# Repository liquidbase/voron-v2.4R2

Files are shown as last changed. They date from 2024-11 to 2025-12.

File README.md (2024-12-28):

# voron v2.4 R2 Pro
Buildlog of voron v2.4 R2 from start to finish with all modifications and finally the toolchanger.

Where possible, corresponding build videos are also included in the readme. When what was done and which files were used will be noted in any case.

# Videolog

# Buildlog
26.11.2024
- Initial Structure for GitHub

15.12. - 23.12.2024
- Printerbuild
- Squaring Gantry

24.12.2024
- Configuration of Klipper
- Squaring Gantry

25.12.2024
- Fixed Motorposition and Stepper
- Squaring Gantry

27.12.2024
- Squaring Gantry

# Configlog
23.12.2024
- Initial config

24.12.2024
- Added UUIDs for documentation
- Heater & fan check with configuration
- Fixed motor pins for Z
- Set homing speed
- Separate macros to own file

25.12.2024
- Splitted Files
- Input Shaper
- Added KAMP
- Thermistor for Chamber
- Fan Control
- Fixed motor settings

27.12.2024
- Update config with new run_current & microsteps
- Update print_start macro

26.12.2024
- Fixed Extrudersettings
- Raised Retries for QDL

27.12.2024
- Added nozzlewiper (by MarcFair)
- Fixed Z-Offset

# Filelog
26.11.2024
- Added formbot specific docs

27.11.2024
- Added PiCam-Mount
- Added Panellatch

01.12.2024
- Added voron assembly manual
- Added CAD file
- Added sample configs for M8P
- Added printfiles for Z-Drives. Z-Idlers & Z-Endstop
- Added 3MF file for Z-Drives
- Added list for parts to print

09.12.2024
- Added printfiles for front idlers
- Added 3MF for front idlers

10.12.2024
- Added printfiles for XY Joints
- Added 3MF for XY Joints

11.12.2024
- Added printfiles for Gantry
- Added 3MF for Gantry

12.12.2024
- Added printfiles for Z-Joints
- Added 3MF for Z-Joints
- Added printfiles for tools
- Added 3MF for tools

22.12.2024
- Added print files for alle parts

23.12.2024
- Added printer.cfg
- Added nevermore print files

24.12.2024
- Added ebb36.cfg

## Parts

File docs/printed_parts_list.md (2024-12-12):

### Voron 2.4 Printed Parts List

List of parts to print for [Voron 2.4](https://github.com/VoronDesign/Voron-2) organized by the [Assembly Manuals](https://github.com/VoronDesign/Voron-2/blob/Voron2.4/Docs/2.4_Assembly_Manual.pdf) order of assembly, allowing for just-in-time printing of parts while building the printer.  Configuration is standard Voron 2.4 (Afterburner Direct Feed, DIN rail mounts) with choices for E3D, Dragon or Mosquito hot ends on a 250mm, 300mm or 350mm frame.  No parts for the drag chain are included, as often these are purchased parts rather than printed.

Names of the sections (such as `Gantry/X_Axis/XY Joints`) match the name of the [STL directory](https://github.com/VoronDesign/Voron-2/tree/Voron2.4/STLs/VORON2.4) that contains the prints.  Note that Voron Design uses filenames starting with `[a]_` at the start of a filename to indicate parts that can be printed in an accent color.

_Credit to [krobertson](https://gist.github.com/krobertson/adfd96689e8b66e7e122705c9ac6bb21) for making a Gist of all parts. This Gist is a modified version of that list, organized by order of assembly, removed parts that don't need printing, identified parts that are optional or specific to a build, and fixed a few incorrect part listings._

--------------------------------------------------------------------------------

### Frame (page 10)

#### [Tools](https://github.com/VoronDesign/Voron-2/tree/Voron2.4/STLs/VORON2.4/Tools)

```
[ x ]  [ x ]   rail_installation_guide_center_x2.stl
```

--------------------------------------------------------------------------------

### Z Drive Assembly (page 18)

#### [Z_Drive](https://github.com/VoronDesign/Voron-2/tree/Voron2.4/STLs/VORON2.4/Z_Drive)

```
[ x ]  [ x ]   [a]_belt_tensioner_a_x2.stl
[ x ]  [ x ]   [a]_belt_tensioner_b_x2.stl
[ x ]  [ x ]   [a]_z_drive_baseplate_a_x2.stl
[ x ]  [ x ]   [a]_z_drive_baseplate_b_x2.stl
[ x ]  [ x ]   z_drive_main_a_x2.stl
[ x ]  [ x ]   z_drive_main_b_x2.stl
[ x ]  [ x ]   z_drive_retainer_a_x2.stl
[ x ]  [ x ]   z_drive_retainer_b_x2.stl
[ x ]  [ x ]   z_motor_mount_a_x2.stl
[ x ]  [ x ]   z_motor_mount_b_x2.stl
```

#### [Z_Idlers](https://github.com/VoronDesign/Voron-2/tree/Voron2.4/STLs/VORON2.4/Z_Idlers)

_There are two different GT20 20T pully files; only one set of them should be printed_

```
[ x ]  [ x ]  [ x ]  [ x ]   [a]_z_tensioner_x4_9mm.stl
[ x ]  [ x ]               z_tensioner_bracket_a_x2.stl
[ x ]  [ x ]               z_tensioner_bracket_b_x2.stl
```

#### [Z_Endstop](https://github.com/VoronDesign/Voron-2/tree/Voron2.4/STLs/VORON2.4/Z_Endstop)

```
[ x ]   nozzle_probe.stl
```

--------------------------------------------------------------------------------

### AB Drive Modules (page 38)

#### [Gantry/Front_Idlers](https://github.com/VoronDesign/Voron-2/tree/Voron2.4/STLs/VORON2.4/Gantry/Front_Idlers)

```
[ X ]   [a]_tensioner_left.stl
[ X ]   [a]_tensioner_right.stl
[ x ]   front_idler_left_lower.stl
[ x ]   front_idler_left_upper.stl
[ x ]   front_idler_right_lower.stl
[ x ]   front_idler_right_upper.stl
```

#### [Gantry/AB_Drive_Units](https://github.com/VoronDesign/Voron-2/tree/Voron2.4/STLs/VORON2.4/Gantry/AB_Drive_Units)

```
[ x ]         [a]_cable_cover.stl
[ x ]  [ x ]   [a]_z_chain_retainer_bracket_x2.stl
[ x ]         a_drive_frame_lower.stl
[ x ]         a_drive_frame_upper.stl
[ x ]         b_drive_frame_lower.stl
[ x ]         b_drive_frame_upper.stl
```

--------------------------------------------------------------------------------

### Gantry (page 46)

#### [Gantry/X_Axis/XY Joints](https://github.com/VoronDesign/Voron-2/tree/Voron2.4/STLs/VORON2.4/Gantry/X_Axis/XY_Joints)

_Select one endstop_pod_* , and one xy_joint_cable_bridge_* depending on your hardware kit_

```
[ x ]   [a]_endstop_pod_microswitch.stl <- select one ^^^ (microswitch XY endstops)
[ x ]   [a]_xy_joint_cable_bridge_generic.stl <= select one vvv (generic drag chain)
[ x ]   xy_joint_left_lower.stl
[ x ]   xy_joint_left_upper.stl
[ x ]   xy_joint_right_lower.stl
[ x ]   xy_joint_right_upper.stl
```

#### [Gantry](https://github.com/VoronDesign/Voron-2/tree/Voron2.4/STLs/VORON2.4/Gantry)

```
[ x ]  [ x ]  [ x ]  [ x ]   [a]_z_belt_clip_lower_x4.stl
[ x ]  [ x ]  [ x ]  [ x ]   [a]_z_belt_clip_upper_x4.stl
[ x ]                     z_chain_bottom_anchor.stl
[ x ]                     z_chain_guide.stl              <-- Not in CAD or documentation
```

--------------------------------------------------------------------------------

### Afterburner (page 58)

#### [Gantry/X_Axis/X Carriage](https://github.com/VoronDesign/Voron-2/tree/Voron2.4/STLs/VORON2.4/Gantry/X_Axis/X_Carriage)

```
[  ]  [  ]   [a]_belt_clamp_x2.stl
[  ]         [a]_blower_housing_front.stl
[  ]         blower_housing_rear.stl
[  ]         hotend_fan_mount.stl
[  ]         probe_retainer_bracket.stl
[  ]         x_carriage_frame_left.stl
[  ]         x_carriage_frame_right.stl
[  ]         x_carriage_pivot_block.stl
```

#### [Gantry/X_Axis/X Carriage/Printheads/E3D V6](https://github.com/VoronDesign/Voron-2/tree/Voron2.4/STLs/VORON2.4/Gantry/X_Axis/X_Carriage/Printheads/E3D_V6)

_Select only one printhead; this is for E3D_

```
[  ]   printhead_front_e3dv6.stl
[  ]   printhead_rear_e3dv6.stl
```

#### [Gantry/X_Axis/X Carriage/Printheads/Slice Mosquito](https://github.com/VoronDesign/Voron-2/tree/Voron2.4/STLs/VORON2.4/Gantry/X_Axis/X_Carriage/Printheads/Slice_Mosquito)

_Select only one printhead; this is for Slice Mosquito_

```
[  ]   printhead_front_mosquito.stl
[  ]   printhead_rear_mosquito.stl
```

#### [Gantry/X_Axis/X Carriage/Printheads/TriangleLab Dragon](https://github.com/VoronDesign/Voron-2/tree/Voron2.4/STLs/VORON2.4/Gantry/X_Axis/X_Carriage/Printheads/TriangleLab_Dragon)

_Select only one printhead; this is for Phaetus Dragon_

```
[  ]   printhead_front_dragon.stl
[  ]   printhead_rear_dragon.stl
```

#### [Gantry/X_Axis/X Carriage/Direct Feed](https://github.com/VoronDesign/Voron-2/tree/Voron2.4/STLs/VORON2.4/Gantry/X_Axis/X_Carriage/Direct_Feed)

_Select the chain anchor (generic or igus) that matches your drag chain choice_ 

```
[  ]   [a]_connector_cover.stl
[  ]   [a]_guidler.stl
[  ]   [a]_latch.stl
[  ]   chain_anchor_generic.stl <-- select one vvv (generic drag chain)
[  ]   chain_anchor_igus.stl    <-- select one ^^^ (igus drag chain)
[  ]   extruder_body.stl
[  ]   extruder_motor_plate.stl
[  ]   latch_shuttle.stl
```

--------------------------------------------------------------------------------

### Belting Z Drive (page 78)

#### [Gantry/Z_Joints](https://github.com/VoronDesign/Voron-2/tree/Voron2.4/STLs/VORON2.4/Gantry/Z_Joints)

```
[ x ]  [ x ]  [ x ]  [ x ]   z_joint_lower_x4.stl
[ X ]                     z_joint_upper_hall_effect.stl <-- if using hall effect XY
[ x ]  [ x ]  [ x ]  [ x ]   z_joint_upper_x4.stl <-- use x3 if using hall effect XY
```

--------------------------------------------------------------------------------

###  LCD Module (page 82)

#### [Electronics_Compartment/LCD_Module](https://github.com/VoronDesign/Voron-2/tree/Voron2.4/STLs/VORON2.4/Electronics_Compartment/LCD_Module)

```
[  ]   [a]_mini12864_case_hinge.stl
[  ]   mini12864_case_front.stl
[  ]   mini12864_case_rear.stl
[  ]   mini12864_spacer.stl
```

--------------------------------------------------------------------------------

### Skirts (page 86)

#### [Electronics_Compartment/Plug_Panel](https://github.com/VoronDesign/Voron-2/tree/Voron2.4/STLs/VORON2.4/Electronics_Compartment/Plug_Panel)

```
[  ]   plug_panel_filtered_mains.stl
```

#### [Skirts](https://github.com/VoronDesign/Voron-2/tree/Voron2.4/STLs/VORON2.4/Skirts)

```
[  ]  [  ]   [a]_60mm_fan_blank_insert_x2.stl
[  ]  [  ]   [a]_belt_guard_a_x2.stl
[  ]  [  ]   [a]_belt_guard_b_x2.stl
[  ]  [  ]   side_fan_support_x2.stl
```

#### [350](https://github.com/VoronDesign/Voron-2/tree/Voron2.4/STLs/VORON2.4/Skirts/350)

_Use these skirts when printing a 350mm frame_

```
[  ]  [  ]   front_rear_skirt_a_350_x2.stl
[  ]  [  ]   front_rear_skirt_b_350_x2.stl
[  ]  [  ]   side_skirt_a_350_x2.stl
[  ]  [  ]   side_skirt_b_350_x2.stl
```

--------------------------------------------------------------------------------

### Panels (page 94)

#### [Panel_Mounting/Front_Doors](https://github.com/VoronDesign/Voron-2/tree/Voron2.4/STLs/VORON2.4/Panel_Mounting/Front_Doors)

```
[  ]  [  ]  [  ]  [  ]   door_hinge_x4.stl
[  ]  [  ]               handle_a_x2.stl
[  ]  [  ]               handle_b_x2.stl
[  ]  [  ]               latch_x2.stl
```

#### [Panel_Mounting](https://github.com/VoronDesign/Voron-2/tree/Voron2.4/STLs/VORON2.4/Panel_Mounting)

```
[  ]  [  ]  [  ]  [  ]                                                   bottom_panel_clip_x4.stl
[  ]  [  ]                                                               bottom_panel_hinge_x2.stl
[  ]  [  ]  [  ]  [  ]  [  ]  [  ]  [  ]  [  ]  [  ]  [  ]  [  ]  [  ]   corner_panel_clip_3mm_x12.stl  <-- 3mm no foam, 6mm w/foam
[  ]  [  ]  [  ]  [  ]                                                   corner_panel_clip_6mm_x4.stl   <-- print either the 3mm or
[  ]  [  ]  [  ]  [  ]  [  ]  [  ]  [  ]  [  ]  [  ]  [  ]  [  ]  [  ]   midspan_panel_clip_3mm_x12.stl <-- the 6mm set 
[  ]  [  ]  [  ]                                                         midspan_panel_clip_6mm_x3.stl  <--  
[  ]  [  ]                                                               z_belt_cover_a_x2.stl
[  ]  [  ]                                                               z_belt_cover_b_x2.stl
```

--------------------------------------------------------------------------------

### Spool Holder (page 102)

#### [Spool_Management](https://github.com/VoronDesign/Voron-2/tree/Voron2.4/STLs/VORON2.4/Spool_Management)

```
[  ]   bowen_retainer.stl
[  ]   spool_holder.stl
```

--------------------------------------------------------------------------------

### Exhaust Filter (page 106)

#### [Exhaust_Filter](https://github.com/VoronDesign/Voron-2/tree/Voron2.4/STLs/VORON2.4/Exhaust_Filter)

```
[  ]         [a]_filter_access_cover.stl
[  ]  [  ]   [a]_exhaust_filter_mount_x2.stl
[  ]         exhaust_filter_grill.stl
[  ]         exhaust_filter_housing.stl
```

--------------------------------------------------------------------------------

### Electronics Mounting (page 112)

#### [Electronics_Compartment/DIN_Brackets](https://github.com/VoronDesign/Voron-2/tree/Voron2.4/STLs/VORON2.4/Electronics_Compartment/DIN_Brackets)

_There are a number of different brackets here depending on your electronics selection._

```
[  ]  [  ]         duet_duex_bracket_x2.stl
[  ]               lrs_psu_bracket_clip.stl
[  ]  [  ]  [  ]   pcb_din_clip_x3.stl
[  ]  [  ]         ramps_bracket_x2.stl
[  ]               raspberrypi_bracket.stl
[  ]               rs25_psu_bracket_clip.stl
[  ]  [  ]         skr_1.3_bracket_x2.stl
[  ]  [  ]         skr_mini_e2_bracket_x2.stl
[  ]  [  ]         skr_mini_e3_bracket_x2.stl
```

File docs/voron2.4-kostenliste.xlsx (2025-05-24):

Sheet: Gesamt
Gesamtkosten
voron 2.4 | 1580.08
Toolchanger | 2022.31
Gesamt: | 3602.39

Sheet: voron 2.4
 |  |  | 1580.08 €
Part | Preis | Bemerkung
Kit | 800.43 € | Startkit
EBB36 | 14.87 € | Dragonburner
Filament | 151.77 € | Verkleidung
Magnetfolie | 51.96 €
Filament | 50.60 € | Verkleidung
Satin Printplate 255x255 | 54.00 € | Druckplatte für X1C zum drucken von PC/PBT
Sherpa Mini Metall Kit | 92.97 € | Extruder
Motor Assembly | 43.13 € | Ersatz
Linear Rail 50mm Tap | 15.00 € | Ersatz
Lüfter | 27.98 € | Ersatz
Kabel | 37.78 € | 220V
Kabel | 49.89 € | Motor
Kabel | 39.97 € | Motor
Bearings | 27.97 € | Gantry-Mod
Phaetus Rapido Plus Hotend 2 HF | 98.99 € | Hotend-Ersatz
Hardend Nozzle 0.4 | 1.99 €
OptoTap | 20.78 € | Ersatz

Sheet: Toolchanger
 |  |  |  |  | 2022.31 €
Part | Menge | Einzelpreis | Preis | Bemerkung
Phaetus Rapido Plus Hotend 2 HF (https://www.3djake.de/phaetus/rapido-plus-hotend-2-hf?sai=15275) | 5 | 98.99 € | 494.95 €
Bondtech OEM Set für Sherpa Mini RIDGA V2 (https://www.3djake.de/bondtech/oem-set-fuer-sherpa-mini-ridga-v2?sai=17363) | 5 | 41.99 € | 209.95 €
Moons Nema 14 Schrittmotor 17mm Dicke 10 Zahn (https://meltbro.de/moon-nema-14-schrittmotor-17mm-dicke-fuer-voron-2-4-sherpa-orbiter-galileo-extruder.html) | 3 | 29.99 € | 89.97 €
MOAR_CAN (https://alchemy3d.de/products/moar_can-8-9-port-can-hub-by-isik-s-tech?_pos=1&_sid=7aa387c65&_ss=r) | 1 | 32.50 € | 32.50 €
BIGTREETECH EBB 36 (https://biqu.equipment/products/bigtreetech-ebb-36-42-can-bus-for-connecting-klipper-expansion-device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) | 4 | 15.75 € | 63.00 €
Filament Runout Sensor | 5 | 9.99 € | 49.95 €
Alu-Extrusions | 1 | 89.29 € | 89.29 € | Top Hat
Igus CANBus Chainflex CF9.02.06 | 1 | 28.79 € | 28.79 €
Kleinteile | 1 | 43.91 € | 43.91 € | Tap Changer
Filament PC/PBT | 4 | 50.99 € | 203.96 €
Filament ASA | 1 | 25.98 € | 25.98 €
Werkzeug | 1 | 49.00 € | 49.00 €
Kleinteile | 1 | 37.63 € | 37.63 € | Stealth Changer
Kleinteile | 1 | 22.04 € | 22.04 € | Silikon, Stahldraht, Federn
Lüfter | 1 | 53.73 € | 53.73 €
Optotap | 5 | 11.79 € | 58.95 €
Alu-Extrusions | 1 | 9.93 € | 9.93 €
Kleinteile | 10 | 0.90 € | 9.00 € | Federstahldraht
Acrylplatten | 1 | 23.79 € | 23.79 € | Top Hat
USB-Hub | 1 | 17.99 € | 17.99 €
TungstenCarbid Nozzle | 5 | 55.00 € | 275.00 €
Flexplate Satin | 1 | 70.00 € | 70.00 €
Flexplate Structured PEI | 1 | 63.00 € | 63.00 €

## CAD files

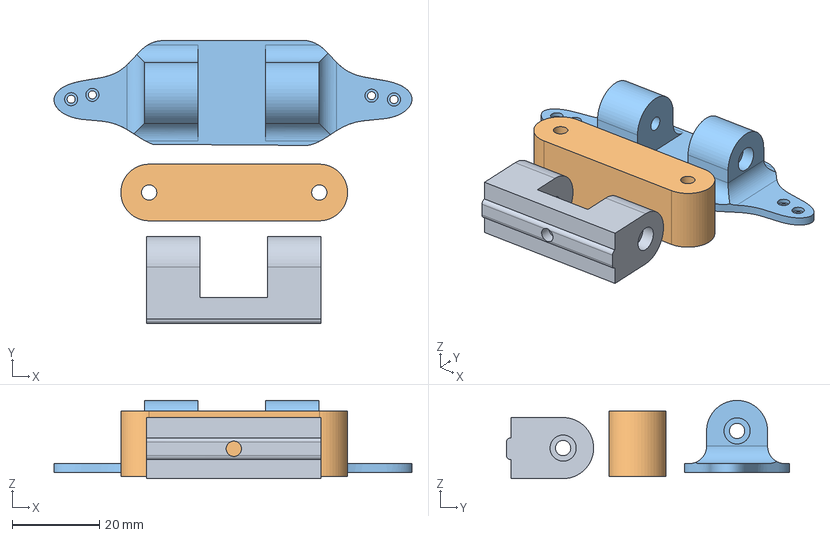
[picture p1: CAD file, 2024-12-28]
printfiles/misc/C92X_PsycHoShafts_Mount by PsychoShaft/CAD/Voron_C92X_Camera_Complete.step
82.1 x 64.9 x 17.9 mm

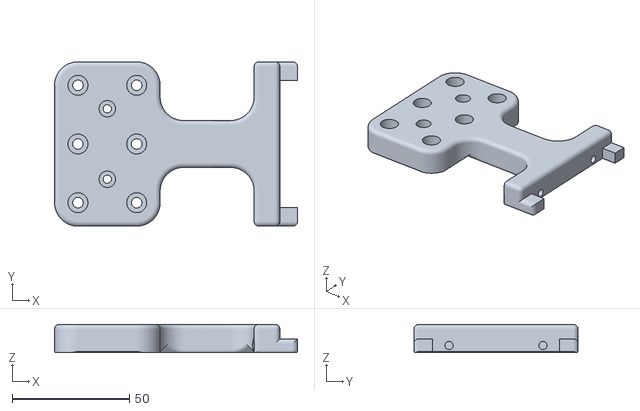
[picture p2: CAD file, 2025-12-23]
printfiles/Toolchanger/DraftShiftCableManagement/UserMods/FlisherOfatale/PTFE_Breakout_Block/Flisher-PTFE_Breakout_Block_Main-v3.1.stl
103.5 x 70.0 x 12.0

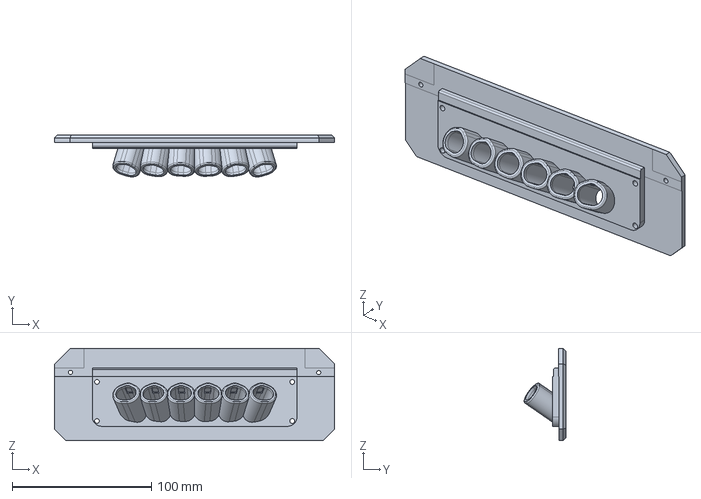
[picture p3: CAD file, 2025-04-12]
printfiles/Toolchanger/DraftShiftCableManagement/UserMods/seenit783/SV08 Umbilical Back Plate/Main Body SV08 Umbilical.step
200.8 x 30.0 x 66.0 mm

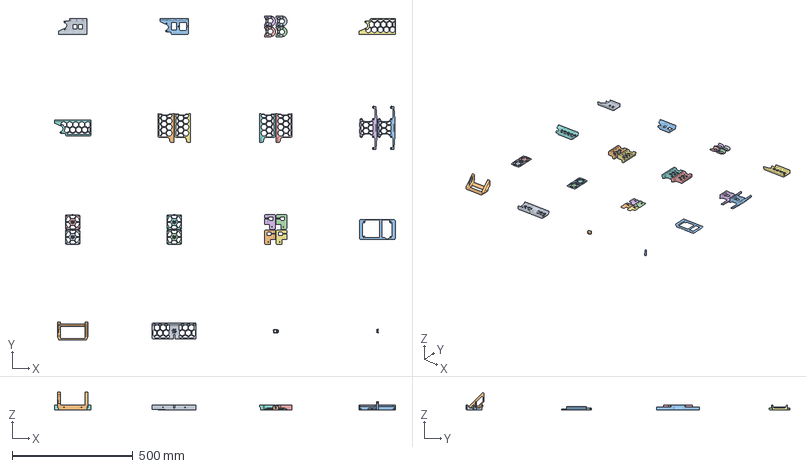
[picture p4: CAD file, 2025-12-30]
printfiles/xx_skirt_assembly.3mf
1410.5 x 1339.9 x 72.4 mm
keystone_panel.stl
BTT HDMI5 V1_2 mount bracket_Regular.stl
btt-hdmi5-v1_2-mount-frame_voron-logo.stl
z_belt_cover_b_x2.stl x 2
[a]_fan_grill_b_x2.stl x 2
z_belt_cover_a_x2.stl x 2
[a]_fan_grill_a_x2.stl x 2
side_fan_support_x2.STL x 2
side_skirt_b_350_x2.stl x 2
side_skirt_a_350_x2.stl x 2
[a]_belt_guard_b_x2.stl x 2
power_inlet_filtered.stl
[a]_belt_guard_a_x2.stl x 2
front_skirt_a_350.stl
front_skirt_b_350.stl
V2 Rear skirt 350 with cable cutout.stl
keystone_wlan.stl
Thermistor_Mount_2020_5mm.stl

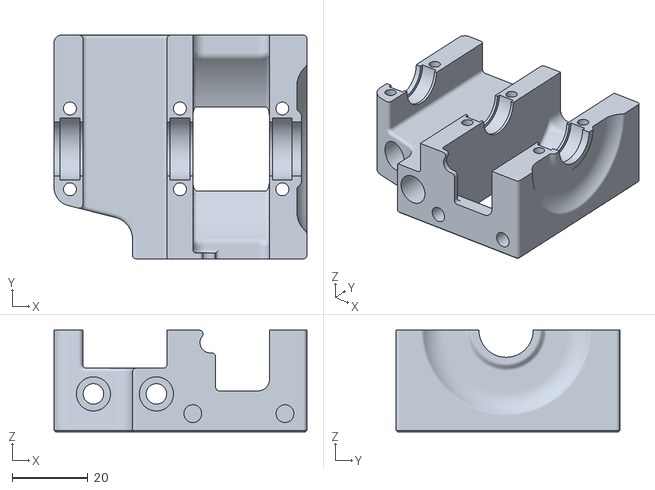
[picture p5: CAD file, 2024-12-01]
printfiles/Z_Drive/z_drive_main_b_x2.stl
66.7 x 59.0 x 26.8

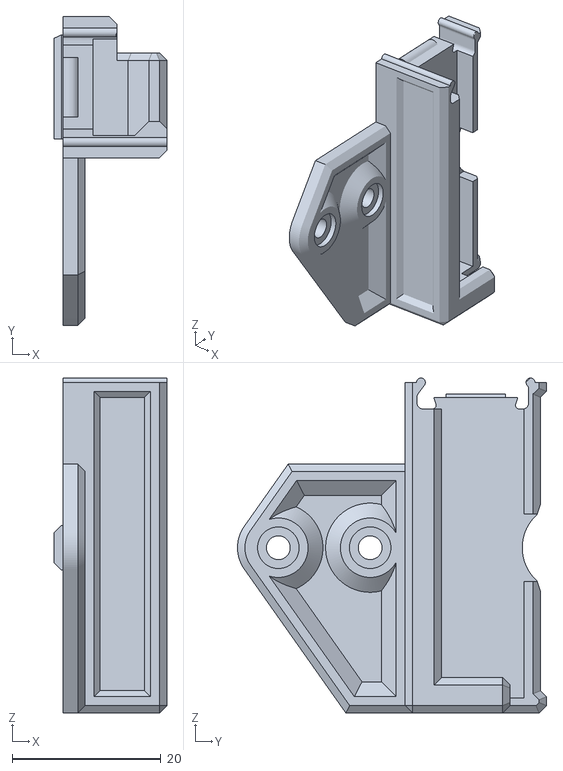
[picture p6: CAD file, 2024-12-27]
printfiles/misc/voron-24-nozzle-cleaning-brush-model_files/nozzle-cleaning-brush-main-body.stl
15.2 x 41.6 x 45.1

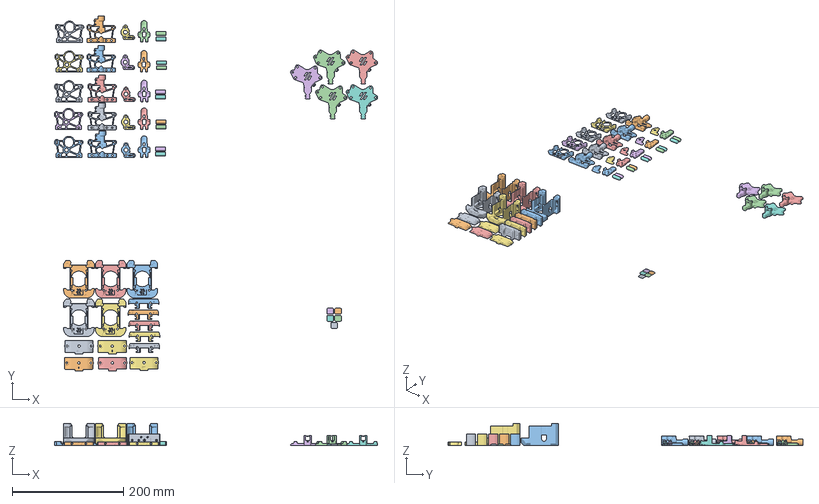
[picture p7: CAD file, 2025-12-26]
printfiles/xx_Toolhead_assembly.3mf
580.7 x 637.5 x 40.0 mm
housing_rear_x1_rev17.STL x 5
[c]_Voron_Diffuser.stl x 5
dragon_cowl_6_magnets_v6.step x 5
EBB_G2SA.step x 5
Sherpa_Mini_Mount.stl x 5
housing_core_std^housing_sherpa_mini_a3_r16(FDM)(FilamentSensor)(ECAS04) x 5
RapidoHF_Mount.stl x 5
18.0mm_oct_universal_spacer.stl x 10
[a]_idler_arm_long_x1_rev16a.STL x 5
[a]_housing_front_x1_rev15.STL x 5

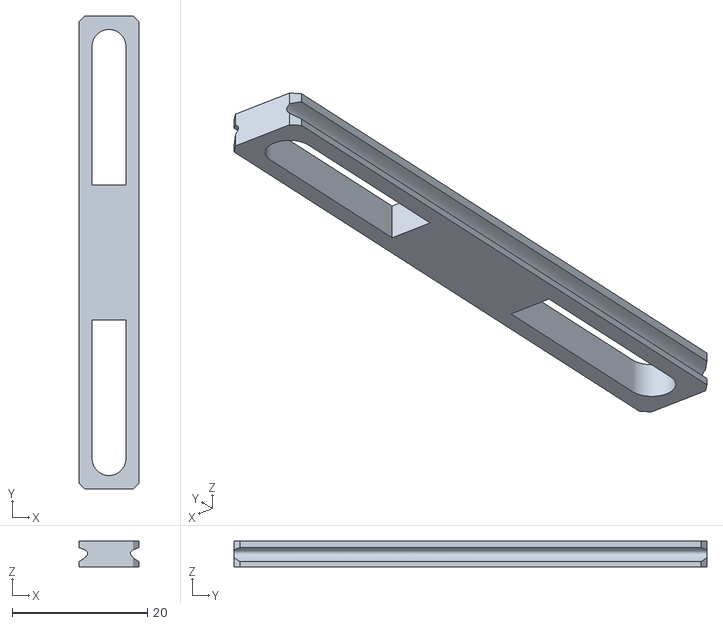
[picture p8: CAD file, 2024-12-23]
printfiles/tap/MGN9_Assembly_Tool.stl
8.90 x 70.0 x 3.80

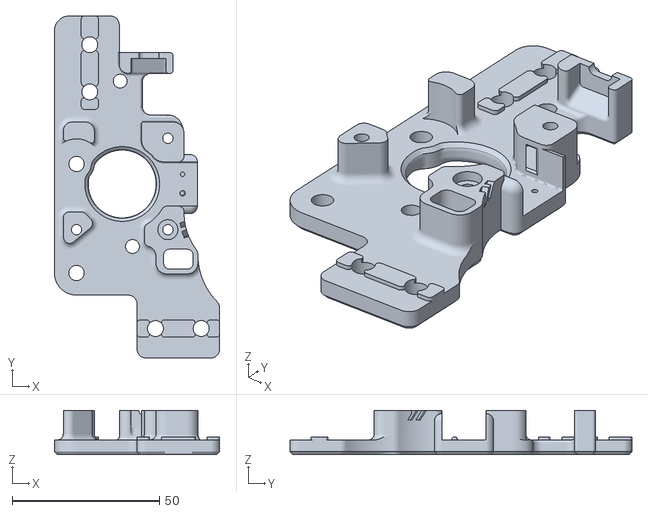
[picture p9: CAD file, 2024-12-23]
printfiles/AB_Drive_Units/a_drive_frame_upper_with_jst_y_endstop.stl
56.0 x 116.0 x 15.0

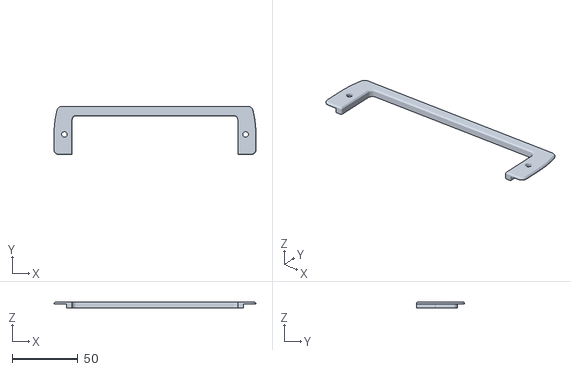
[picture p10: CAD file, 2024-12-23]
printfiles/backplate/Front_Plate.stl
154.0 x 36.8 x 4.60

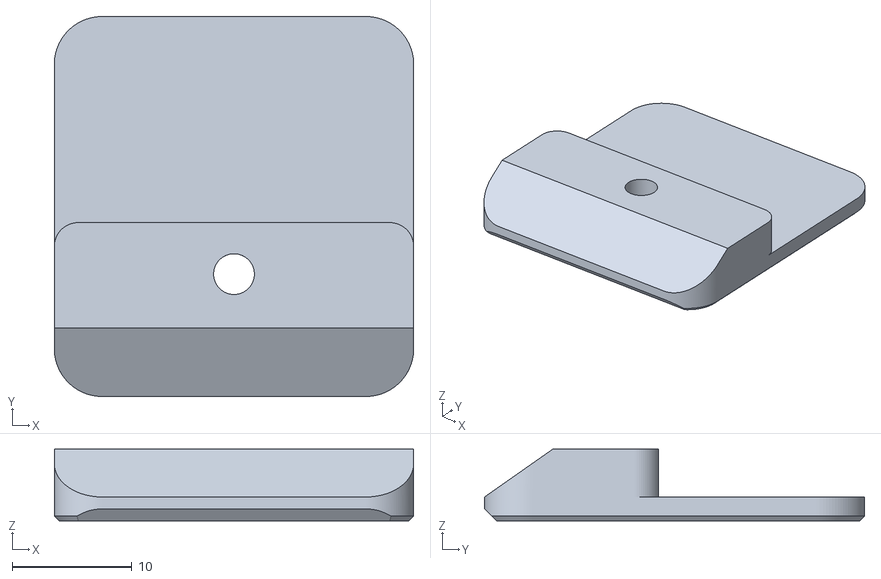
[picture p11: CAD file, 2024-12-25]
printfiles/bottom_panel/bottom_panel_clip_x4.stl
30.0 x 31.7 x 6.00

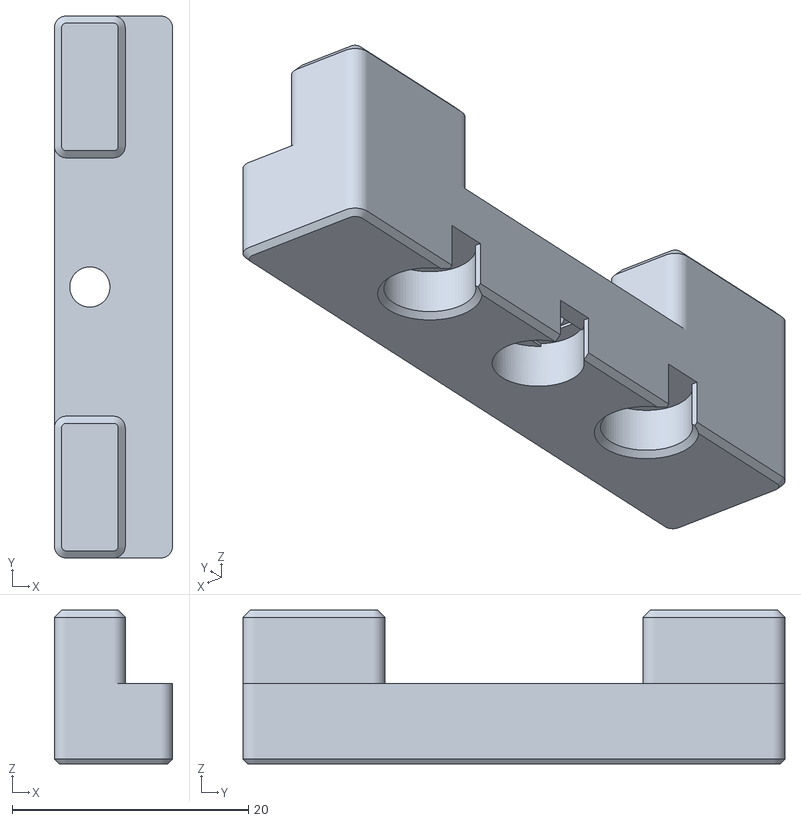
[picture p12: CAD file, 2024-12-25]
printfiles/Doors/latch_x2.stl
10.0 x 45.9 x 13.0

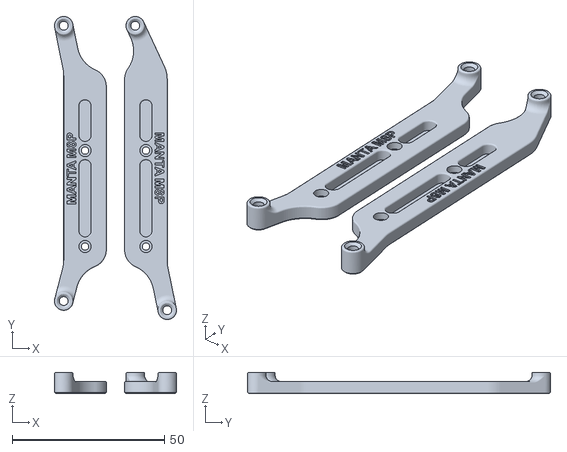
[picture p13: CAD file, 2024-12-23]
printfiles/EBay/Manta_M8P_2pc.stl
40.1 x 99.5 x 7.00

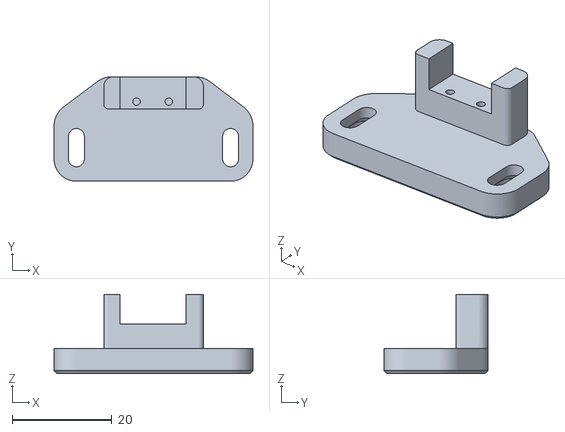
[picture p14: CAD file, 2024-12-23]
printfiles/Endstops/y_endstop.stl
40.0 x 21.0 x 15.9

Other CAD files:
printfiles/Z_Drive/z_drive_main_a_x2.stl
printfiles/Front Idlers/front_idler_right_lower.stl
printfiles/Gantry/[a]_z_belt_clip_upper_x4.stl
printfiles/misc/C92X_PsycHoShafts_Mount by PsychoShaft/STL/C92X_Extrusion_Bracket_No_Support_Required.stl
printfiles/AB_Drive_Units/[a]_cable_cover.stl
printfiles/AB_Drive_Units/[a]_z_chain_retainer_bracket_x2.stl
printfiles/AB_Drive_Units/a_drive_frame_lower.stl
printfiles/AB_Drive_Units/a_drive_frame_upper.stl
printfiles/AB_Drive_Units/b_drive_frame_lower.stl
printfiles/AB_Drive_Units/b_drive_frame_upper.stl
printfiles/Doorbuffer.3mf
printfiles/Doors/Door_Handle_x1.STL
printfiles/Doors/door_hinge_x6.stl
printfiles/Doors/handle_a_x2.stl
printfiles/Doors/handle_b_x2.stl
printfiles/EBay/PSU_stabilizer_50mm.stl
printfiles/EBay/Printed_Part_for_CAN_Cable_V1.2.stl
printfiles/EBay/lrs_200_psu_bracket_x2.stl
printfiles/EBay/pcb_din_clip_x3.stl
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

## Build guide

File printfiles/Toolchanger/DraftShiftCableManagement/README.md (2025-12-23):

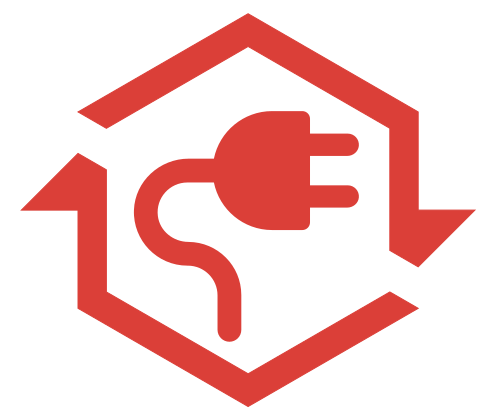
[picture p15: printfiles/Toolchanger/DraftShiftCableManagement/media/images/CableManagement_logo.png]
#  CableManagement


&nbsp;&nbsp;&nbsp;&nbsp;&nbsp;&nbsp;


Backpacks, Umbilicals, and general cable management projects
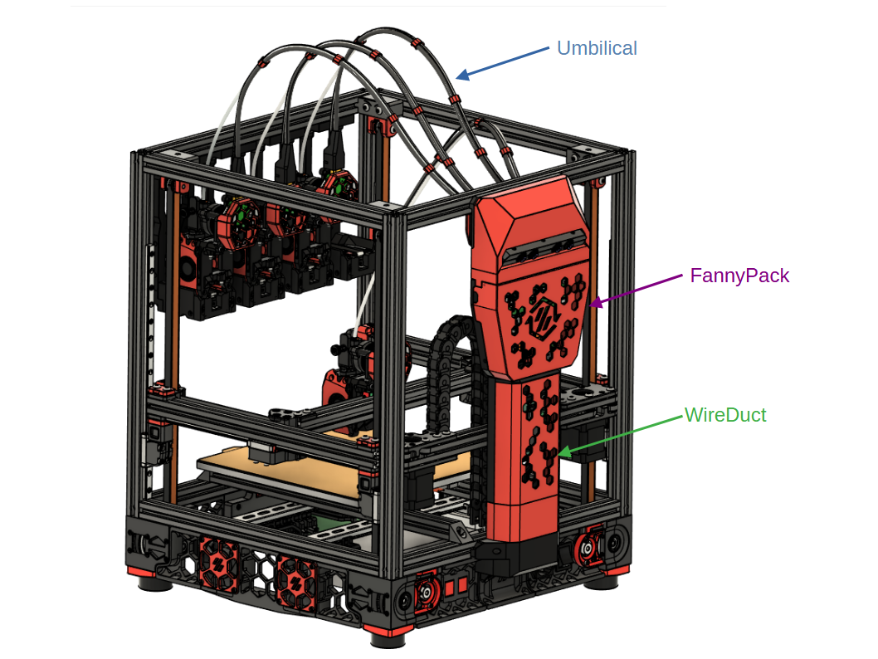
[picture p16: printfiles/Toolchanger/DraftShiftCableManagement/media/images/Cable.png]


This repo will be a collection of different options.  Feel free to use the one that you prefer.

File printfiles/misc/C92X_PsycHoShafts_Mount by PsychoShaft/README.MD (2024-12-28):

# Important Notes

Hello everyone,

Here is my C920 camera mod, please follow the disasembly guide below to remove the current mount off the camera. Please keep the 4 bottom screws from the mount as you will need them for my mod.

# Instructions For Disassembly

[Found Here!](https://www.ifixit.com/Guide/Logitech+C920+Webcam+Disassembly/115077)
#

This mod allows you to set 2 point postion for your camera, 

## BOM

Qty | Item
:-- | :--
2 | M3x40mm
1 | M3x10mm
2 | Nuts
1 | M3 Hammerhead nut



# Photos of finished build below

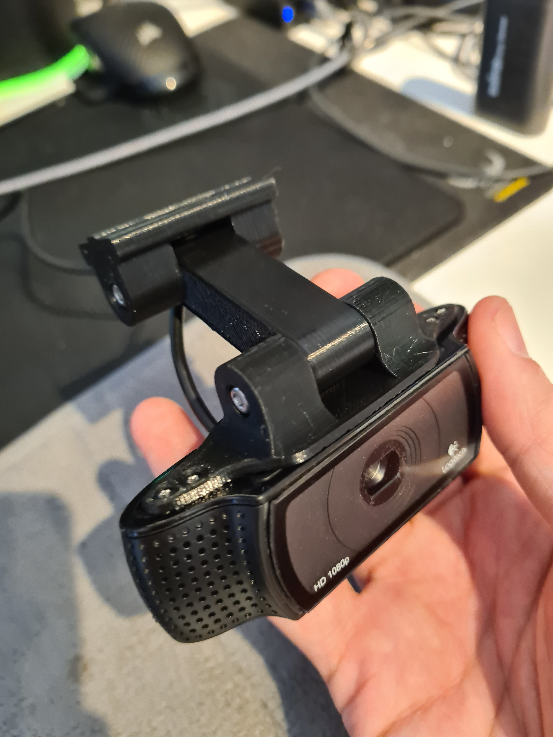
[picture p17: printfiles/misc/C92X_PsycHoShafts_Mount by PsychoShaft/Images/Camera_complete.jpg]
 
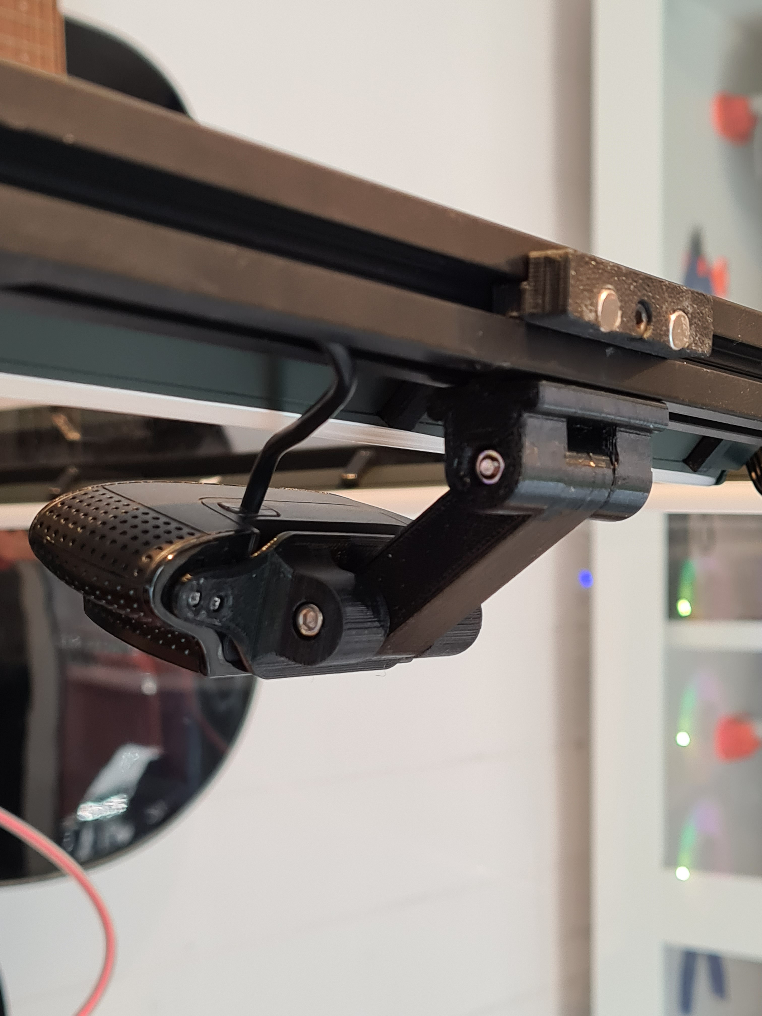
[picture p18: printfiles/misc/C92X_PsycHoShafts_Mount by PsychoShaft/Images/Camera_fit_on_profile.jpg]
 
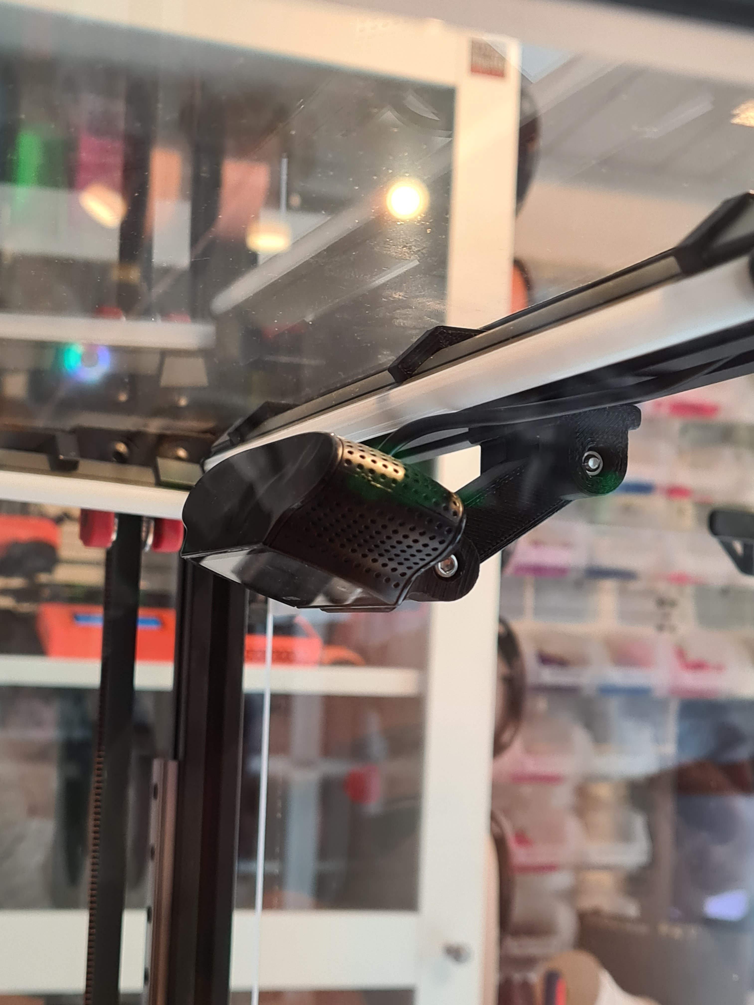
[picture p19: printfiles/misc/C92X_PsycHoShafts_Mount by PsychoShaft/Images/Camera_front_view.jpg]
 
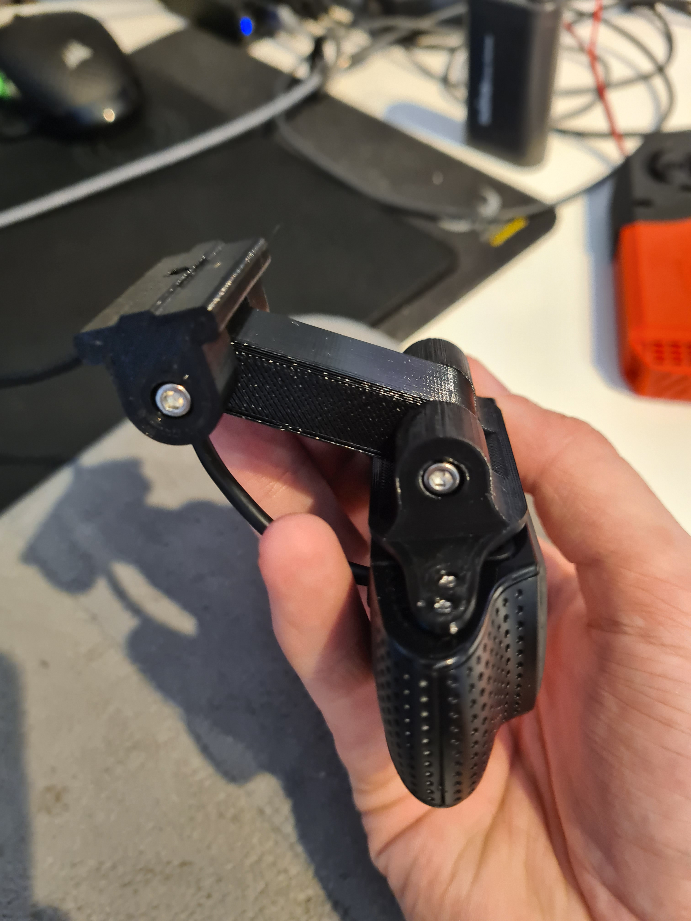
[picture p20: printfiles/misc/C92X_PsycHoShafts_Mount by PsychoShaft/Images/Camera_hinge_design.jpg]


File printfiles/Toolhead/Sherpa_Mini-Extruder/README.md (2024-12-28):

## Sherpa Mini - Release 2:

This release adds support for Bondtech's RIDGA v2 in addition to numerous tweaks and updates to make the extruder easier to work on and more reliable than ever. 

## Changelog

+ Bondtech RIDGA v2 compatibility (R2 RC1 and newer)
+ Bondtech insert support
+ Stronger and stiffer idler arm
+ Increased clearance between idler arm and core
+ Minor fixes and adjustments in preparation for upcoming upgrades

+ Core housing and rear housing need to be reprinted if upgrading from Release 1
+ Updated idler arms are backwards compatible with Release 1 and Release 2 RC1

## FAQ
For Material Requirements, Print Settings and How to Interpret the file naming structure, please see: "Print_Settings_and_File_Key.txt"

The BOM and Sourcing Guide for this product can be found here: https://docs.google.com/spreadsheets/d/1O3eyVuQ6M4F03MJSDs4Z71_XyNjXL5HFTZr1jsaAtRc/edit?usp=sharing

## Product Info
This is the Sherpa Mini Extruder, a ground up design developed by Anlin and the team at Annex Engineering. It's a dual geared hobbed filament extruder designed for use with any printer. It features a gear driven design to provide torque while being able to be near silent. You must perform your own tuning to get the best results.

A Pinion Equipped Pancake Stepper is required for this Release.

Our discord server can be found here: 

Join me on Discord (https://discord.gg/MzTR3zE)

Please only use GitHub Issues for repo and file related problems. For general design related questions and technical support please visit our Discord server.

Image of Sherpa Extruder

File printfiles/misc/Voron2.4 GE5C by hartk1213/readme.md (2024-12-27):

# Voron 2.4 GE5C Z joint  

##

### BOM
Screws			
|Size|Qty|
|---|---|
|M3x12 |4|
|M3x16 or M3x20 SHCS|16|	
|M5x20 |4|	
|Ge5C Bearing|4|
|M5x1mm spacer|4|
|If using Halleffect 6x3 magnet | 1 |

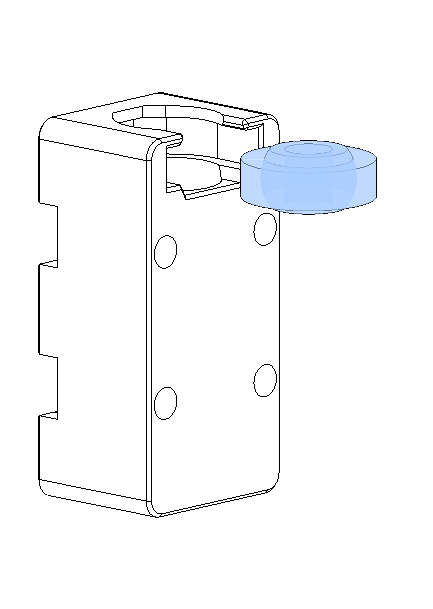
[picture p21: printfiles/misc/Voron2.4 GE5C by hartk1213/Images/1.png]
 

First just insert GE5C bearing , it should just pop in

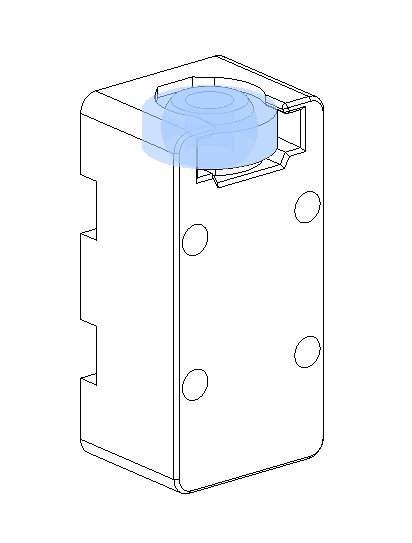
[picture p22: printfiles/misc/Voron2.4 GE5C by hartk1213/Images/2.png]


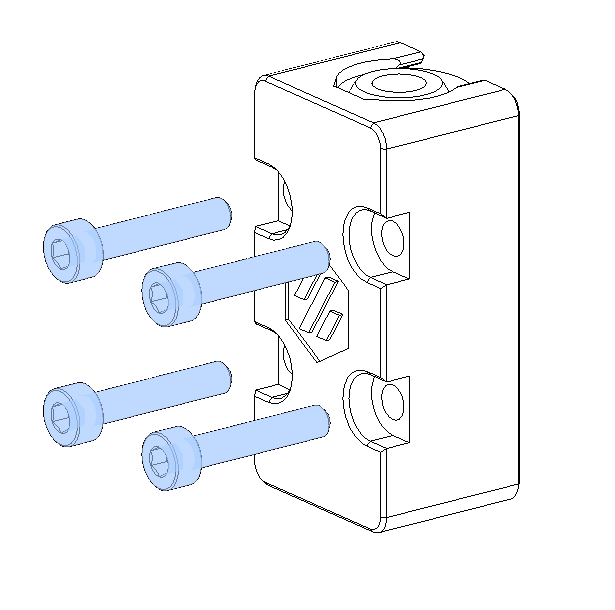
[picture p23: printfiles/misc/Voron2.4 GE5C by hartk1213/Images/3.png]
 

Now if you are using the "slim" version you need 4 m3x16 screws per z joint, if you are using the standard or hall effect version then you need 4 m3x20 per z joint.

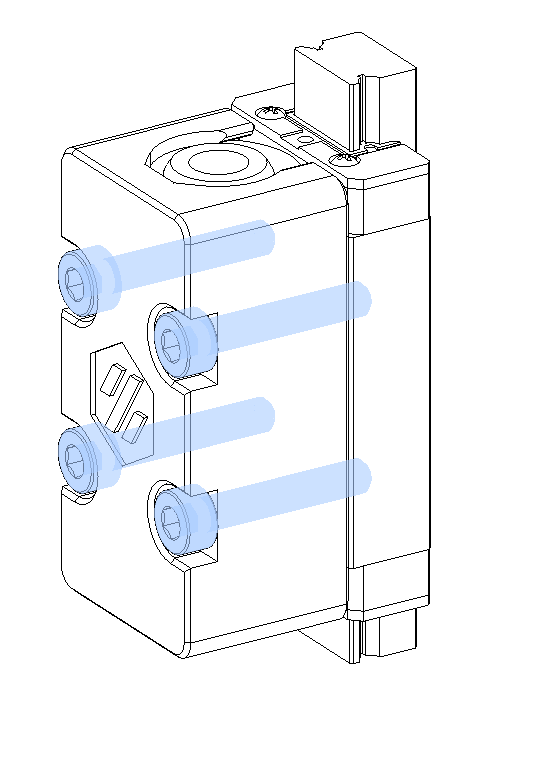
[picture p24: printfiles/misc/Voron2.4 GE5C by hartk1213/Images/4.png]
 

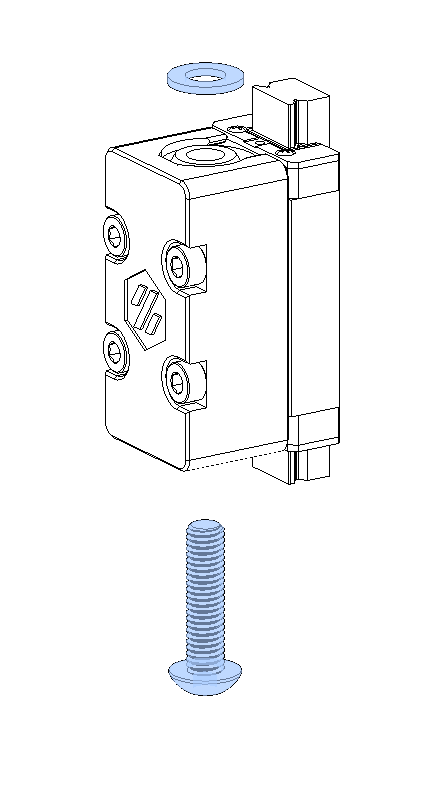
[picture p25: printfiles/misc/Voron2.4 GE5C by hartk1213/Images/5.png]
 

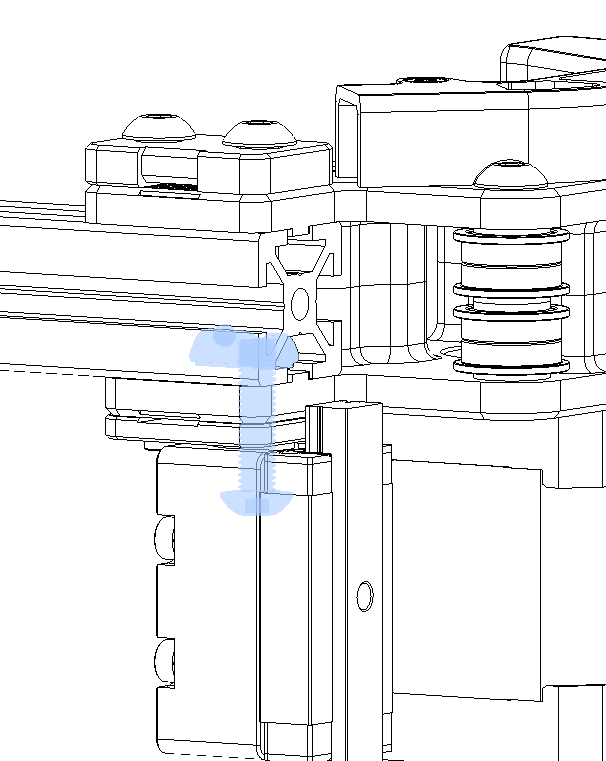
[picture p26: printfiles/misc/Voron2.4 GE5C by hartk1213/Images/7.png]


Use an M5x20 BHCS and 1 m5x1mm washer and screw it into the gantry using a roll in tnut

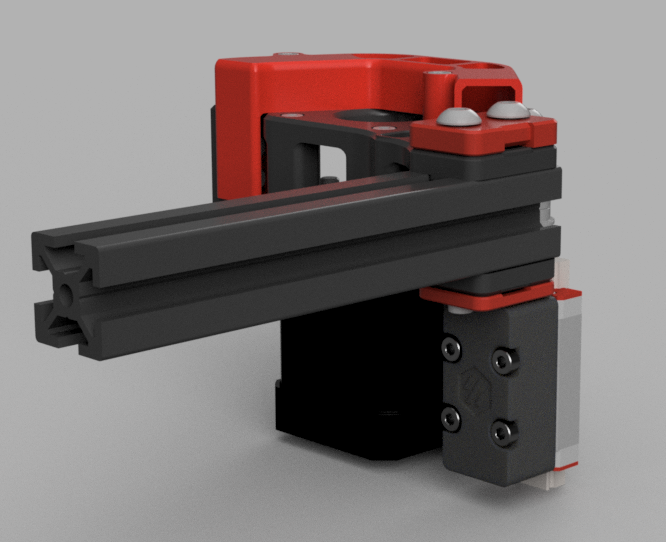
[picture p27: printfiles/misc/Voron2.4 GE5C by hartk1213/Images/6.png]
 

This is how it should be assembled when all done

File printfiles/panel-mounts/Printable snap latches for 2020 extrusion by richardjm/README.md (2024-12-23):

# Printable quick release latch for panels on 2020 extrusion

*I wouldn't say no to a like and a make on printables if you're that way inclined -
https://www.printables.com/model/172368-voron-24-filament-latch-or-any-2020-extrusion*

## Intro

This is originally inspired by a youtube video - [https://www.youtube.com/watch?v=6p7M18oPn3k](https://www.youtube.com/watch?v=6p7M18oPn3k)

Another user is creating cad and variants - [https://github.com/v6cl/My-Voron2.4-Customs/tree/main/Panel_Locker](https://github.com/v6cl/My-Voron2.4-Customs/tree/main/Panel_Locker)

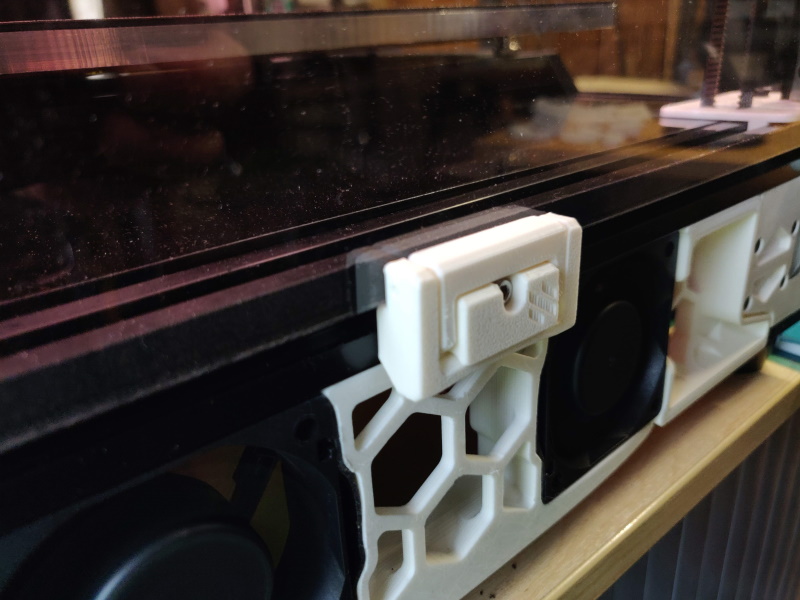
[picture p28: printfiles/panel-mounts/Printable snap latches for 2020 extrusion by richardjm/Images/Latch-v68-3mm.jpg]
Latch


## So why did you do it?

1. I wanted a variant with filament hinges
1. I found it didn't put quite enough pressure on the panel and my attempts to moodify the cad failed
1. Decided the best way to understand it was to design it
1. Wanted adjustable "pressure" and thought using a sweep on the latch was a nice solution making the most of the flex of ABS
1. Wanted everything as a parameter so I could tune it
1. Build plate density, a bonus of using a filament hinge is that the area used for each hinge is much smaller

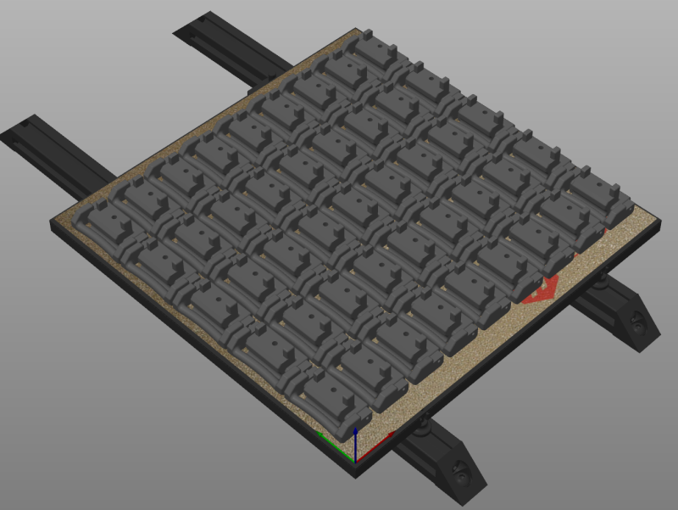
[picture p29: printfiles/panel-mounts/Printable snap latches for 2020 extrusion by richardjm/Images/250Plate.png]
250Plate


45 instances on a 250 buildplate

## Hardware
- 3.0mm-5.5mm - m3x12
- 6.0mm-8.0mm - m3x16
- 8.5mm - m2x20

## The process

1. Cad attempt one failed, just modified surfaces to create a filament variant but adjustement beyond that failed
1. Cad attempt two failed, created a traced version copying the dimensions but again couldn't get a reliable adjustment
1. Cad attempt three of the cad sketch made as built was finally onto something, took until v45 before I had something that seemed to fulfil my requirements, then after thinking overnight revisited earlier designs and finally hit RC at v68 (18 actually printed)
1. Final design and thankfully discovered [sheeter](https://n3rdlab.com/downloads/sheeter/) which allows me to produce many stls based on parameters

## Assembly



1. Print parts (do test prints to ensure you're happy with the fit before going wild)
1. Assemble to correct orientation
1. Insert two short filament lengths connecting middle hinge to hinge body, one from each side
1. Insert one long filament length connecting middle hinge to outer hinge
1. The filaments are a tight-ish fit on the hinge arms but loose in the pivot intentionally
1. Connect to frame using with hammer nut or spring loaded nut with either m3x12 or mx16 depending on size of hinge printed

## Parameters

To make your own custom hinges you can modify the parameters in the cad - via Modify -> Change Parameters. Removing the logo just requires
you to supress the logo extrusion (last extrusion in the first group).

Changing these parameters to extremes may either not work or require fixups of chamfers and fillets, or even the primary sketch.

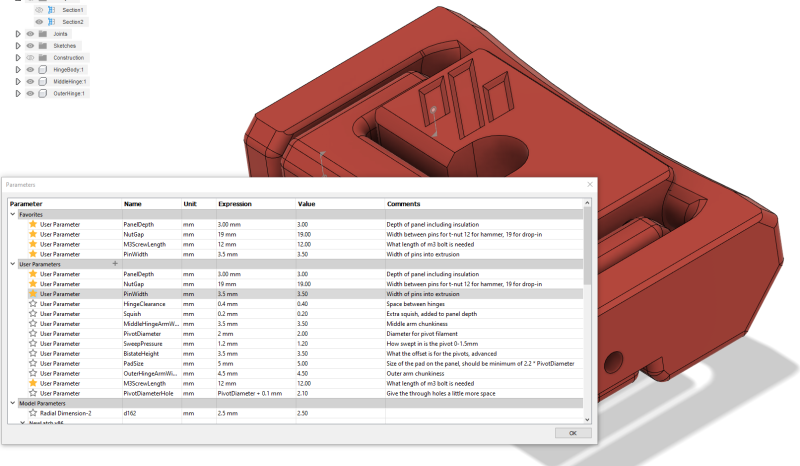
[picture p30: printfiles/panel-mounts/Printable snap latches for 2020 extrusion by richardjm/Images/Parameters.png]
Parameters


Once done, adjust the build plate view (use top view to ensure clearance) and save the file as mesh.

BuildPlate

## Changes
2022-02-11: Added detent from devincody
2022-07-29: Reworked sketch to resolve in Fusion 360, re-exported fixing some incorrect sizes

discord:whistlinric

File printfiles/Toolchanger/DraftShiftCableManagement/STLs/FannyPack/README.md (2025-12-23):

# Fanny Pack

Originally created by [EddieSha04](https://github.com/EddieSha04) aka [ManCheetah](https://www.printables.com/@EddieSha_454383) and adopted by DSD.

## DSD Changes

- Removed fans.
- Added modular mount system for PCBs.
- Added modular sub mount system for WAGOs and other boards.
- Added 2 places for [Mini DC-DC Buck Converters](https://www.aliexpress.com/item/32729546380.html).
- Added micron cover.
- Rotated hexes so they match all other project orientation.
- Make the hex spacing a uniform partern.

## Images

| Open | Closed |
| :-: | :-: |
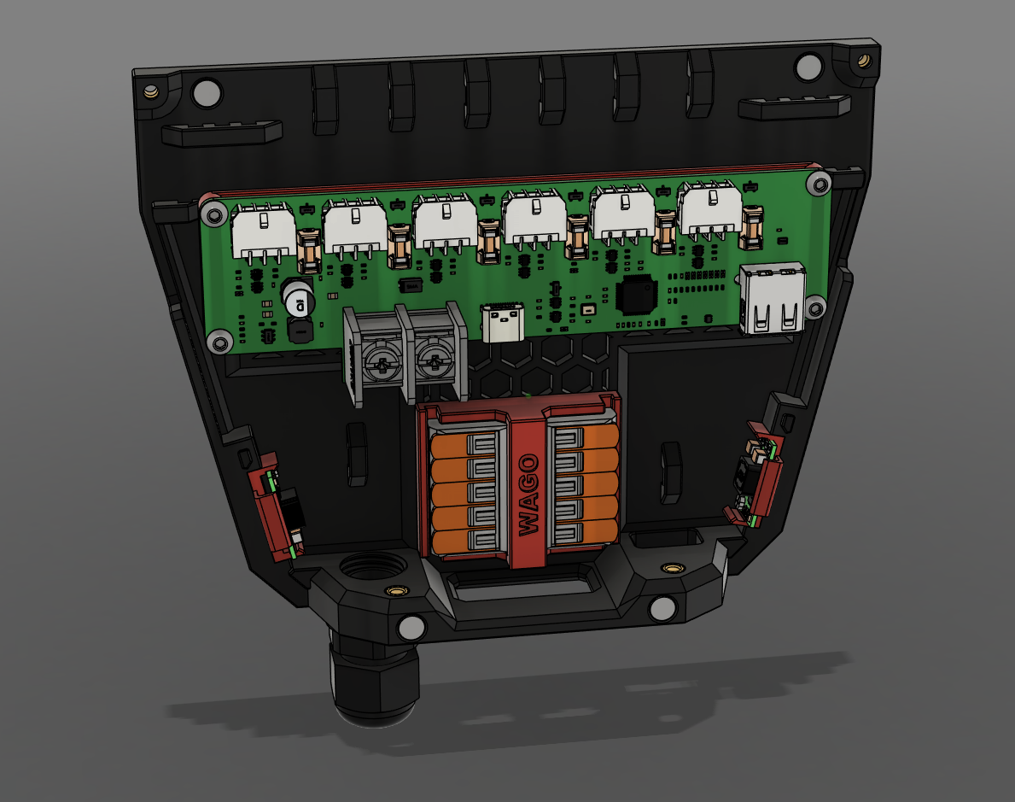
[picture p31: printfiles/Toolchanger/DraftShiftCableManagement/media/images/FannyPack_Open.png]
Open
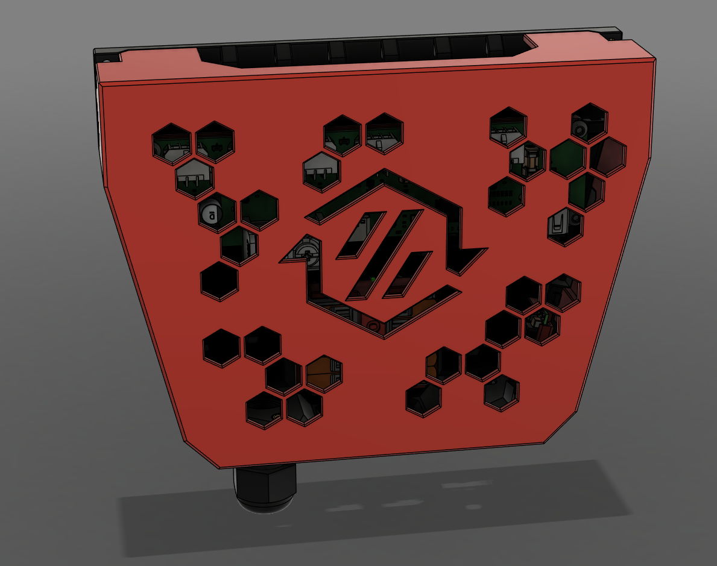
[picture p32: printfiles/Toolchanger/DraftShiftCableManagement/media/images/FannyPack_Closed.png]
Closed
|  |  |

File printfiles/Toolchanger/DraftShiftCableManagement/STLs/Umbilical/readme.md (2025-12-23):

# Umbilical System

Originally created by [N3MI](https://github.com/N3MI-DG) and adopted by DSD.
The Original can be found [here](../../UserMods/N3MI-DG/Umbilical_plates_V2/).
## DSD Changes

- Added PTFE Ramp for FannyPack integration.
- Adapted Cover to attach to ramp and include ECAS mount.

## Images

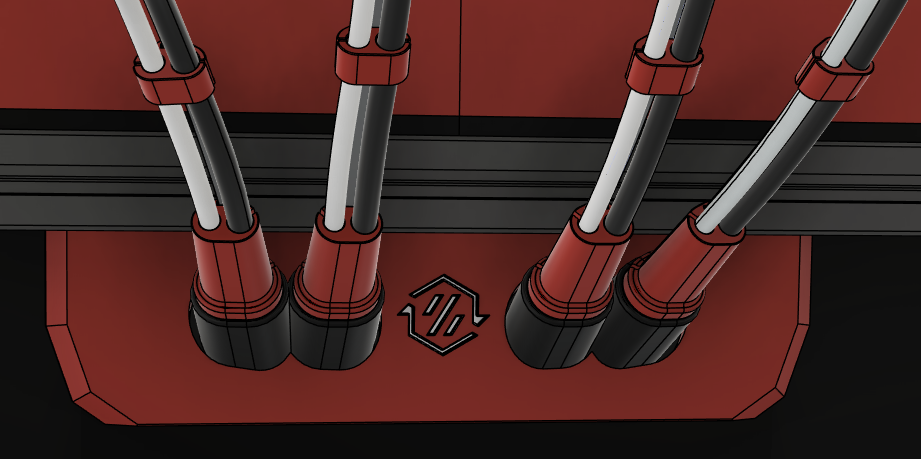
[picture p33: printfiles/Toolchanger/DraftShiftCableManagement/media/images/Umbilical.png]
Umbilical


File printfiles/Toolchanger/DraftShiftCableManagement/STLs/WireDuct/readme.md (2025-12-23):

# Wire Duct

## Features

- Attaches to FannyPack and rear skirt for clean cable management.
- Included EMS panel for additional extension.
- Scales to suit any size printer.

## Images

| Outer | Inner |
| :-: | :-: |
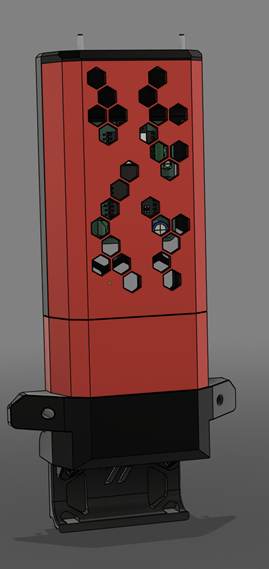
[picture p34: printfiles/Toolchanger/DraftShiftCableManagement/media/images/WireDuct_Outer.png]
Outer
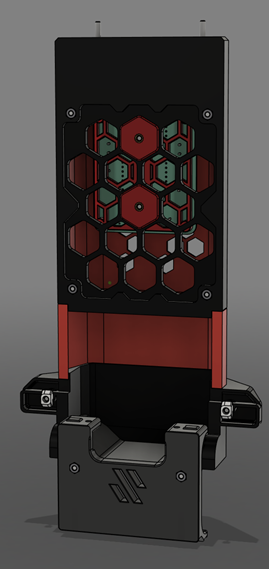
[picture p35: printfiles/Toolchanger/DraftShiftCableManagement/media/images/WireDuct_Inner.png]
Inner
|  |  |

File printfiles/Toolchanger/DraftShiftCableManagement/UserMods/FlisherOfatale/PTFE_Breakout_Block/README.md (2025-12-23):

# PTFE Breakout Block

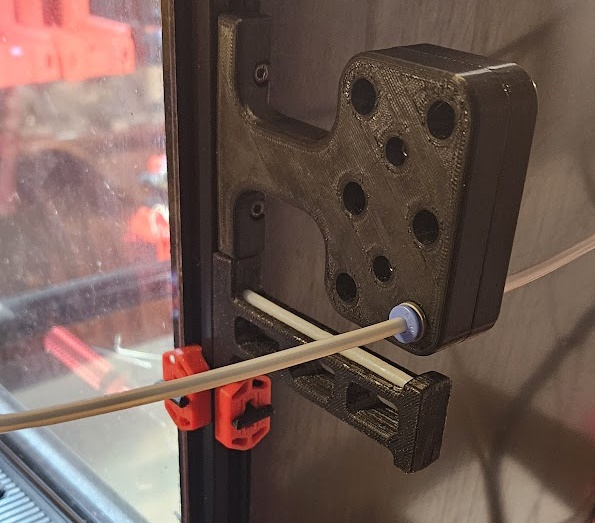
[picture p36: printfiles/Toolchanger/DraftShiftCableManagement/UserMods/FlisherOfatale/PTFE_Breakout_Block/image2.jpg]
PTFE Breakout Block


## What is it?
I designed the Breakout Block with the following idea in mind:
* Similar "lenght" than the stock Voron Spool Holder so it maintain existing clearance for people using the original setup
* Provide some constrain to the PTFE so it doesn't king when using 3mm innder diameter
* use ECAS because they are practical for this purpose
* Optional, seconary part that serve as a breakout block, allowing to "detach" easily both side of the block to decouple the toolhead and the spool holder when doing printer maintenance

## Special Notes
The design is probably not perfect but it was good enought for me at this point.

## Files
* [Main part v3.1](Flisher-PTFE_Breakout_Block_Main-v3.1.stl)
* [Secondary Part v3.1](Flisher-PTFE_Breakout_Block_Secondary-v3.1.stl)
* [Step File](Flisher-Toolchanger-PTFE-Holder-v3.1.STEP)

## BOM
* 2x M3 T-Nuts or Roll-in Nuts
* 2x M3x12 SHCS Screws 
* 1x ECAS Connector per Lane you want activate

If using both parts
* 2x M3x16 SHCS Screws (Voron Sandard)
* 2x M3 heat insert (Voron Sandard)
* Additional 1x ECAS Connector per Lane you want activate (ie: 12 totals if using 6 toolheads)

## Instructions
### Main Part
* Validate that your PTFE can go trought easily, if not, you might have to deburr rthe side facing the bed.
* Install the ECAS connectors
* Screw to the back of the printer using M3 T-Nuts and M3x12 SHCS Screws

You can stop here if you only wanted something to constrain the filament path and use it as a passtrought

### Secondary part
* Validate that your PTFE can go trought easily, if not, you might have to deburr rthe side facing the bed.
* Install the ECAS connectors
* Install the 2 heats inserts (on the same side than the ECAS connector)
* Install on the main block by using 2x M3x16 SHCS Screws
* Push the PTFE coming from the main part as it can get 2mm inside 
* Attach the PTFE from the printer side
  
You now have a setup you can decouple by pulling the filament back to the spool holders and unscrewing the block.

### Additional Pictures
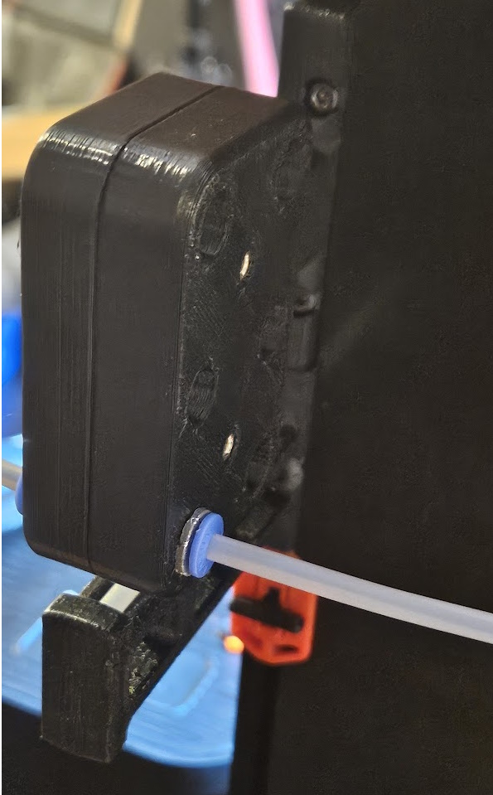
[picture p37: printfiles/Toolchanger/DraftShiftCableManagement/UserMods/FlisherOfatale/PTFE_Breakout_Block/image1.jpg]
Secondary Partg


## Changelog
* V3.1 2024-03-24 - Initial Release, each parts are 12mm wide

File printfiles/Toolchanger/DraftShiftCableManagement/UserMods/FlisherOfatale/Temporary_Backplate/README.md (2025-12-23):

# Temporary Backplate

## What is it?
Very rought backplate that support some electronic, it's naked, not intented to be a final solution, but a good placeholder while working on other stuff.
This is not intended to be your final setup, but is a nice placeholder while figuring everything out.

## Feature
* Allow 4x 5+3 WAGO slot
* 2 Zip Tie Channel to secure the USB and 24V/GND wiring
* Slot for a USB2CAN

## BOM
* 4x M3 Heat Insert
* 4x M3 Screws

## Special Notes
This is not a perfect design, but it allow to work, use WAGO even if it's your final goal, and play with wiring.

# DISCLAIMER
You need to be carefull to not short stuff while playing around, always shut down power with the switch before touching stuff with this.

## Files
* [Backplate v2 - STL File](Flisher-Temporary_Backplate-V2.STL)
* [Backplate v2 - Step File](Flisher-Temporary_Backplate-V2.STEP)

## Credits:
The original idea come from **gdachs** Backpanel showcased on the Voron Tool Change Discord server, but my version is independant from the exaust port.
Original design can be found at https://cad.onshape.com/documents/60014468b9b72e460b456067/w/f3137b097c5c1d080a4612b0/e/ff5c83f39f6ad8db1b8a2981

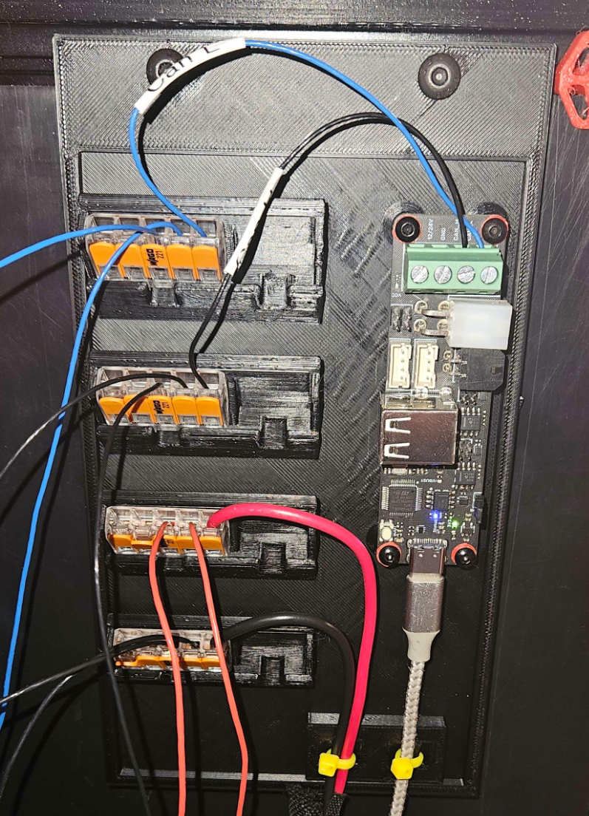
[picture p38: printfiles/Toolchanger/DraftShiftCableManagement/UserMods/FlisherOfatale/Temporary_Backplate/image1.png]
Temporary Backplate


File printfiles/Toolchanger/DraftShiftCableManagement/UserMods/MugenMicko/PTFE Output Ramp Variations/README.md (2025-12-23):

# PTFE Output Ramp Variations  
Single, Double, Triple, Four, Five and Six Way Variations for the PTFE Ramp on FannyPack
These are to be used in conjunction with N3MI's backplate. When I went to use this, I found that the PTFE I/O didn't align with the output ramp
which would cause very tight bends in the PTFE which would cause excessive drag on the filament.  In a bid to resolve this, I relocated the PTFE
Ramp Coupler positions to make them as straight as possible.  This requires no additional hardware than would be used for the original.

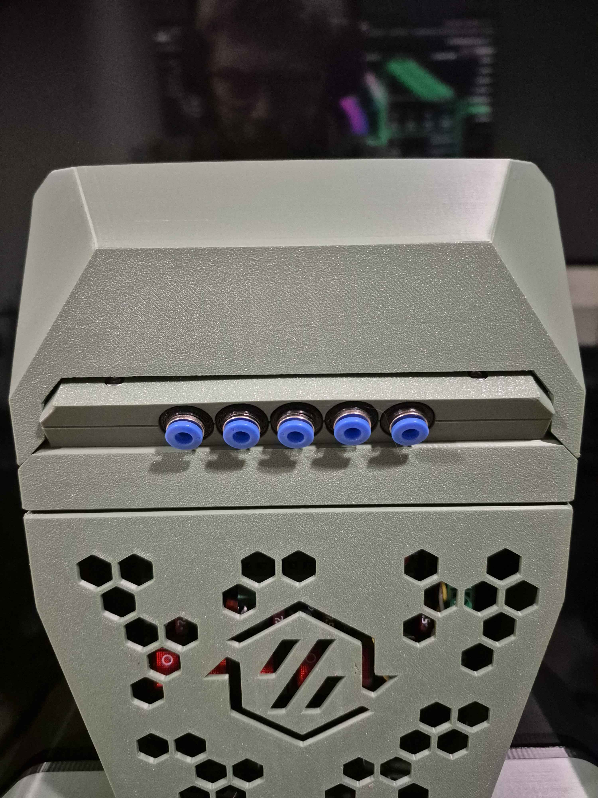
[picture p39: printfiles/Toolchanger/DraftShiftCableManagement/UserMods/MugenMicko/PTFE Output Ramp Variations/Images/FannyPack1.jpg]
FannyPack1

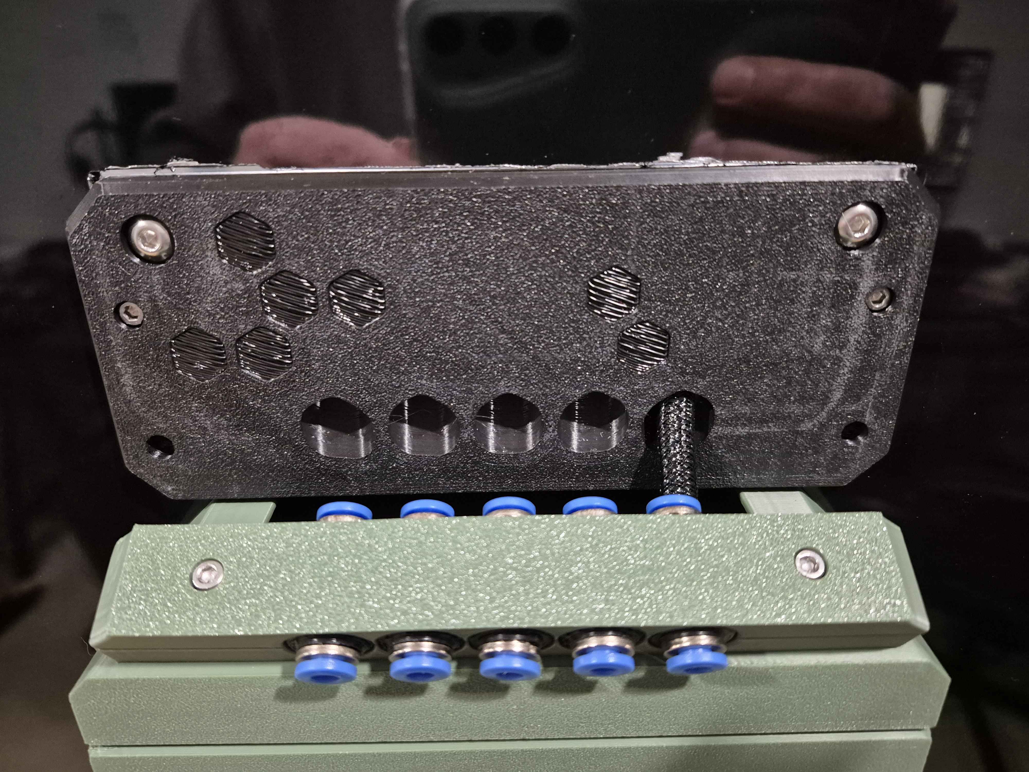
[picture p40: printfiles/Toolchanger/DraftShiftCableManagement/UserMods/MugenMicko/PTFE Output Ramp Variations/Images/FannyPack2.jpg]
FannyPack2


# Credits
- [N3MI-DG](https://github.com/N3MI-DG) for the Filament Entry Design this is based on

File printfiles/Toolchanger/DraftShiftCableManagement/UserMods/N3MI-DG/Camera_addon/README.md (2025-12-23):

# Umbilical Plate Camera Addon
This addon is suitable for 250, 300 and 350 spec Voron Stealthchangers.

## BOM

- [OV5640 USB Camera Module](https://www.aliexpress.com/item/1005004703285622.html)
- 2x M2x10 Self Tapping Screws
- 2x M3x8 SHCS Screws
- 2x 2020 M3 Drop-in T-nuts

## Instructions

### Step 1

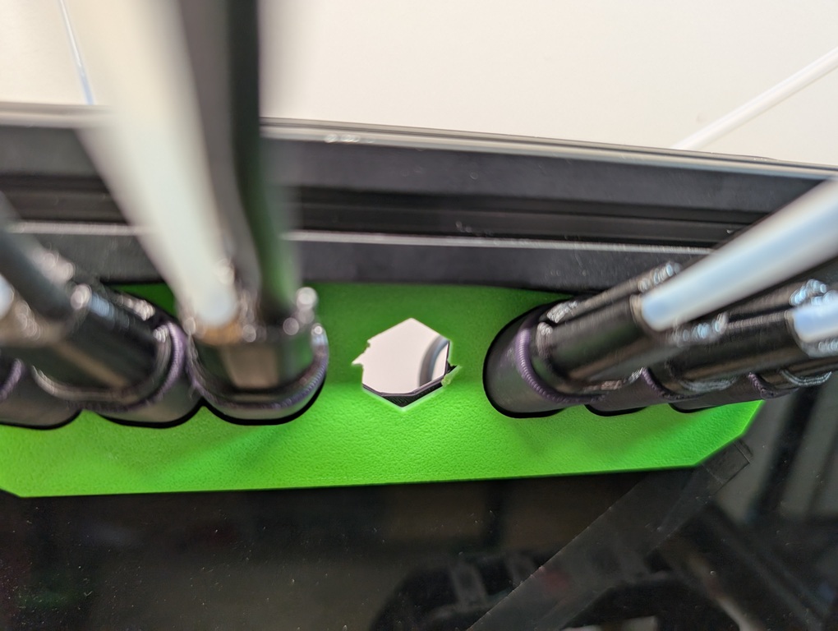
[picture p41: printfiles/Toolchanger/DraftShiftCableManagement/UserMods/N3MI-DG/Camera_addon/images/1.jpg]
Step 1


- If upgrading an existing setup, undo all the screws in the back plate and remove the existing insert before snipping out the logo.

- New installs should snip out the logo before anything is assembled.

### Step 2

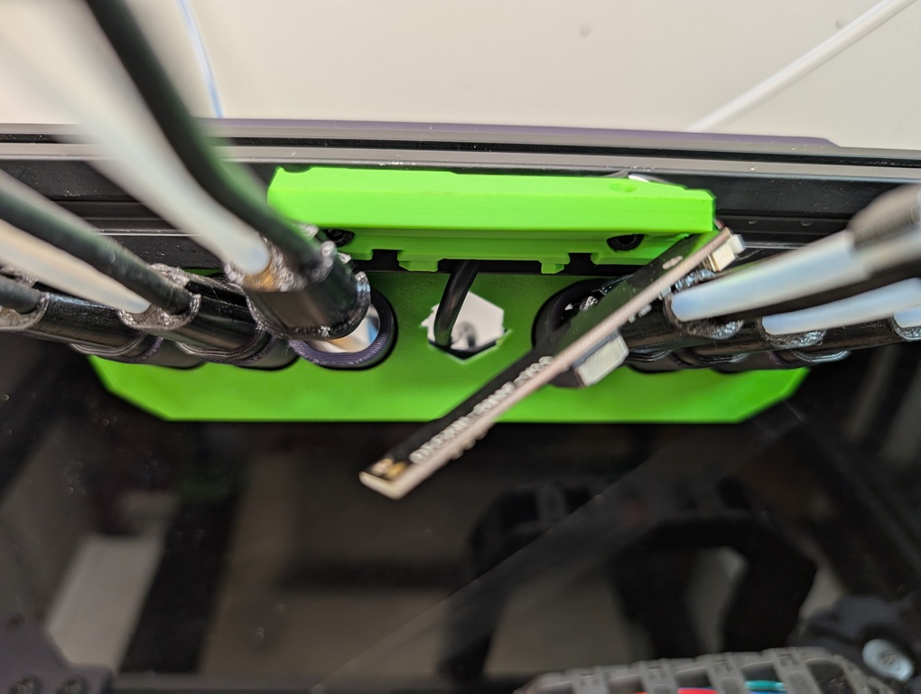
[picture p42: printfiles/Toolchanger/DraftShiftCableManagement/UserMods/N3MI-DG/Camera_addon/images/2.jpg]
Step 2


- Attach the camera mount loosely with the 2 M3x8 SHCS screws and 2020 M3 drop-in T-nuts making sure the cable is routed behind the mount and through the hole of the umbilical plate.

### Step 3

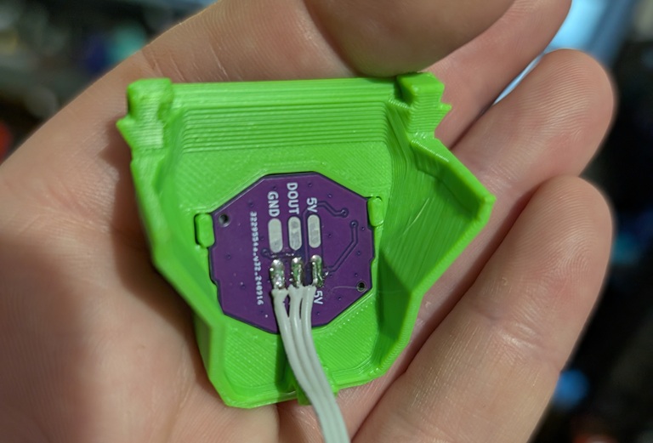
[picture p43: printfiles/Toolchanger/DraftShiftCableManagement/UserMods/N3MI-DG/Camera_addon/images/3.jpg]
Step 3


- Install the insert to the lower cover and SC Barf LED if you have it. There are locating tabs on the insert piece, take not of their orientation.

### Step 4

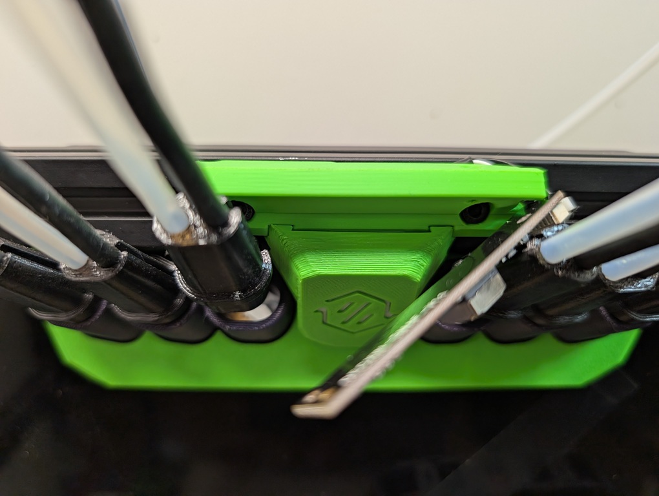
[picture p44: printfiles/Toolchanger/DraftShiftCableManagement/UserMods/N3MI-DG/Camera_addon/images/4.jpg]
Step 4


- Install the lower cover ensuring the bottom tab is locked into the hole in the umbilical plate and the upper locating tabs are seated in the corresponding reliefs on the camera mount. This will center the camera. Once centered, tighten the 2 M3x8 SHCS screws.

### Step 5

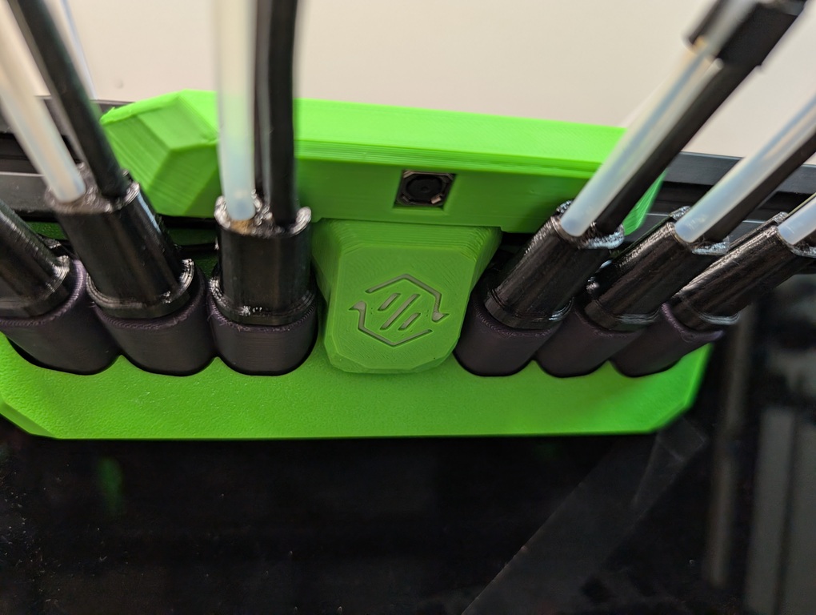
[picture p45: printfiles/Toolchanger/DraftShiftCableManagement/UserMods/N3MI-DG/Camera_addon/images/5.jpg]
Step 5


- Sandwich the camera between the upper cover and camera mount and then install the 2 M2x10 self tapping screws from the top.

### Example image on a 300 Spec Voron

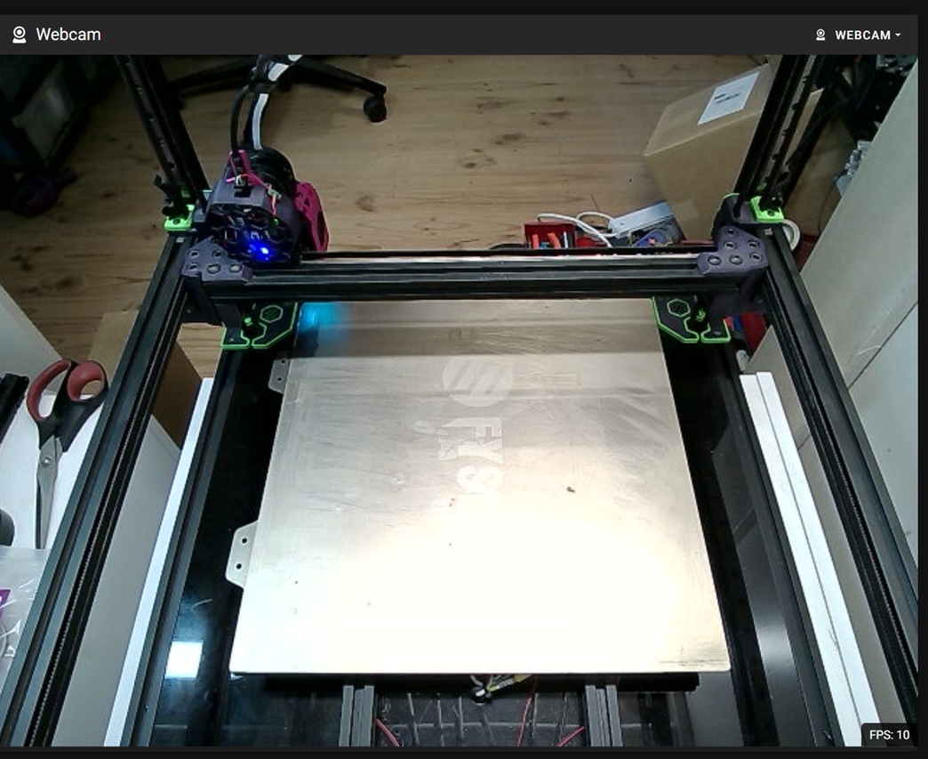
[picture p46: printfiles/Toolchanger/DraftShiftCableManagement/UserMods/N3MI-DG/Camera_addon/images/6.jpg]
Example


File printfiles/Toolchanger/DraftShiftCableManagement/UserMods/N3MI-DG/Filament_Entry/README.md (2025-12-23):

# Toolchanger Filament Entry

There are many different combinations that are possible for this mod. Pick what suits you best.

Measure the depth of your panel to frame before printing and choose between the 3, 3.5, 4, 4.5 & 5mm versions.
Choose how many tools to support. You can print multiple to have Bowden tubes exit either side of the printer for example.
Choose the version you want, there are 2 to choose from. Split and Solid.
The solid version is complete and can be printed in 1 piece.
The split version gets printed in separate pieces and then assembled (Better for multiple colours).

[CadQuery](https://github.com/CadQuery/cadquery, "CadQuery") source code is also available.

## BOM

- ECAS04 for each tool
- M3x20 SHCS screws (3 for 6 tool, 1 for 2 tool and 2 for the rest)
- M3 hammer nut (3 for 6 tool, 1 for 2 tool and 2 for the rest)

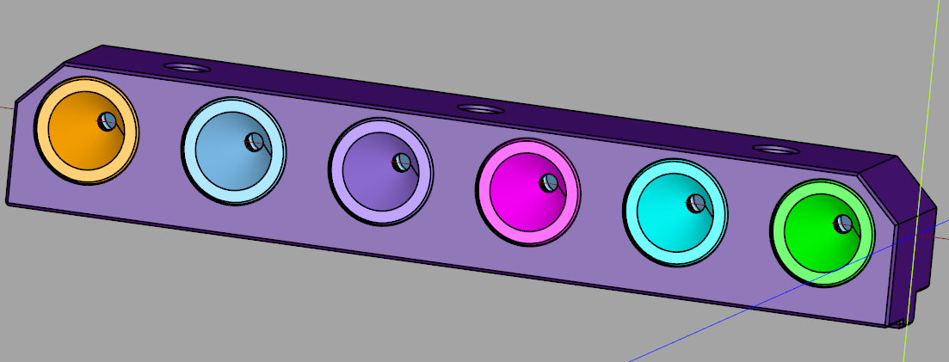
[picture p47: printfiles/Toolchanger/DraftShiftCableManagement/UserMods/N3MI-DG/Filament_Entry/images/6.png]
Six

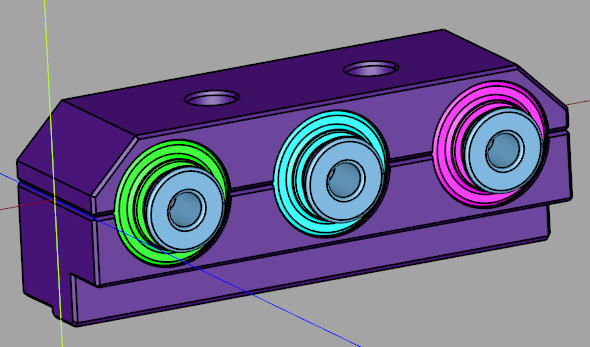
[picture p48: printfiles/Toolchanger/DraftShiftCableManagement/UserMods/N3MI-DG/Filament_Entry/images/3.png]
Three

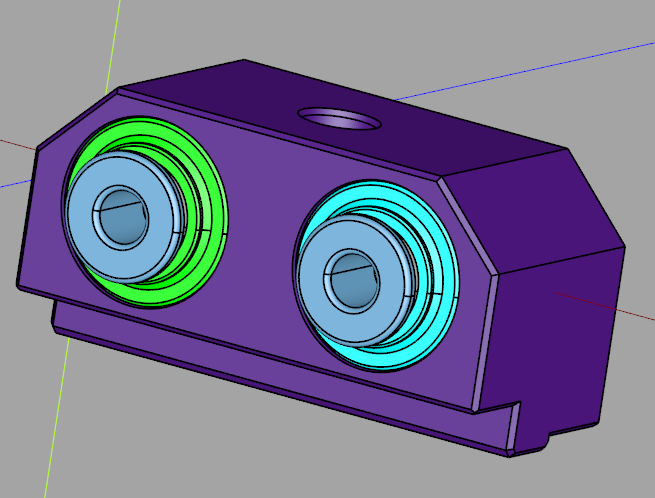
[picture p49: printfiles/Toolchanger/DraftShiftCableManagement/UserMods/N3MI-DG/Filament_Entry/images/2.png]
Two

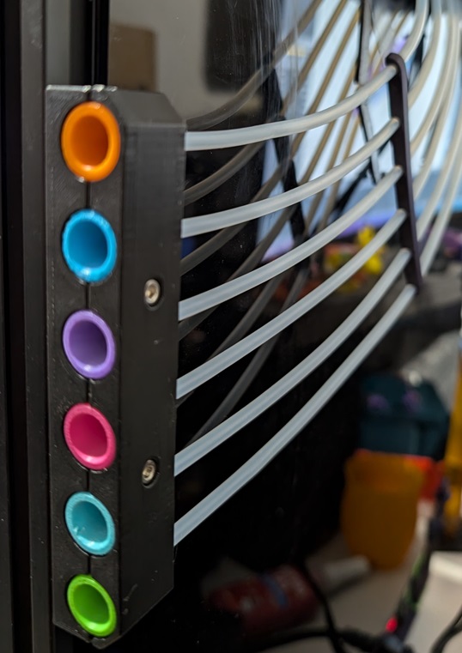
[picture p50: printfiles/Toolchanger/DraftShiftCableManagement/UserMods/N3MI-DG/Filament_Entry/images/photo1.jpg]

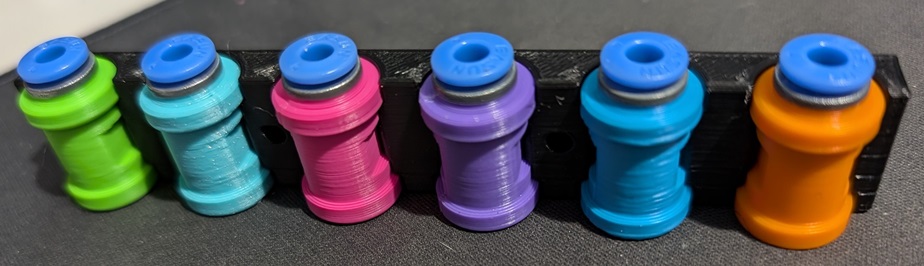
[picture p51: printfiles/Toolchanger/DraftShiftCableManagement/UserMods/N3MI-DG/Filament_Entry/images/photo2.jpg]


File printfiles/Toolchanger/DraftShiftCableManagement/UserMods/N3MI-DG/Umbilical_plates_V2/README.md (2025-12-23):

# Umbilical System for StealthChanger
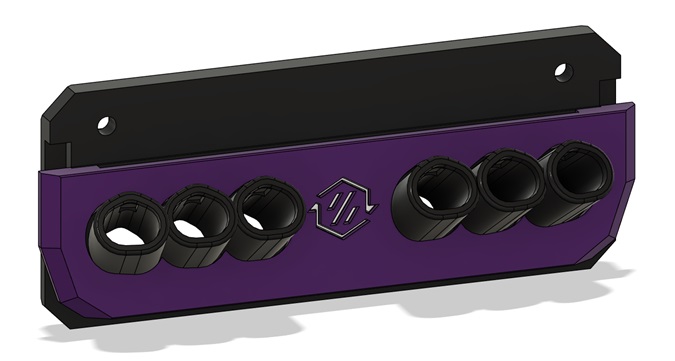
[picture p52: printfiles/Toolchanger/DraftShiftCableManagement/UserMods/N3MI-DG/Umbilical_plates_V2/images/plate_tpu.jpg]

## Introduction
This umbilical system is ultimately made up of 2 components. The "Umbilical Plate" which mounts to the rear panel of your Voron V2 or Micron printer and the "Umbilical Restraints" that help tame the umbilical on its way to the tool head.
There are various combinations on how these components can be configured, choose wisely.
## Umbilical Plate
To choose the appropriate umbilical plate for your setup there are 6 things to consider.
- The type of printer you have.
- The size of the printer.
- The amount of tools you want to support.
- The type of umbilical you are using, TPU or Threaded.
- The width of the docks for the tools you are using.
- How the docks are positioned on the printer, Left, Right, Centered or Split.

The docks play a big role in this system and based on which tools you are using there can be 2 different nominal dock widths.

###### 60mm Nominal Width Docks
- Anthead
- Dragon Burner
- Mini StealthBurner
- Yavoth

###### 76mm Nominal Width Docks
- A4T
- Archetype Blackbird
- StealthBurner
- XOL

From the below tables, select the appropriate umbilical plate configuration for your setup.
<details name="printers">
<summary style="cursor: pointer;">Voron 250mm TPU 60mm Wide Dock</summary>

### Voron 250mm TPU 60mm Wide Dock
| Tool Count | Left | Right | Center | Split |
|-|-|-|-|-|
| 2 |[](STL/Plates/Voron/250/2%20Tools/60mm%20Wide%20Dock/TPU/Left/) |[](STL/Plates/Voron/250/2%20Tools/60mm%20Wide%20Dock/TPU/Right/) |[](STL/Plates/Voron/250/2%20Tools/60mm%20Wide%20Dock/TPU/Center/) |[](STL/Plates/Voron/250/2%20Tools/60mm%20Wide%20Dock/TPU/Split/) |
| 3 | - | - |[](STL/Plates/Voron/250/3%20Tools/60mm%20Wide%20Dock/TPU/Center/) |[](STL/Plates/Voron/250/3%20Tools/60mm%20Wide%20Dock/TPU/Split/) |
| 4 | - | - |[](STL/Plates/Voron/250/4%20Tools/60mm%20Wide%20Dock/TPU/Center/) |[](STL/Plates/Voron/250/4%20Tools/60mm%20Wide%20Dock/TPU/Split/) |
| 5 | - | - | - |[](STL/Plates/Voron/250/5%20Tools/60mm%20Wide%20Dock/TPU/Split/) |

</details>

<details name="printers">
<summary style="cursor: pointer;">Voron 250mm TPU 76mm Wide Dock</summary>

### Voron 250mm TPU 76mm Wide Dock
| Tool Count | Left | Right | Center | Split |
|-|-|-|-|-|
| 2 |[](STL/Plates/Voron/250/2%20Tools/76mm%20Wide%20Dock/TPU/Left/) |[](STL/Plates/Voron/250/2%20Tools/76mm%20Wide%20Dock/TPU/Right/) |[](STL/Plates/Voron/250/2%20Tools/76mm%20Wide%20Dock/TPU/Center/) |[](STL/Plates/Voron/250/2%20Tools/76mm%20Wide%20Dock/TPU/Split/) |
| 3 | - | - |[](STL/Plates/Voron/250/3%20Tools/76mm%20Wide%20Dock/TPU/Center/) |[](STL/Plates/Voron/250/3%20Tools/76mm%20Wide%20Dock/TPU/Split/) |
| 4 | - | - | - |[](STL/Plates/Voron/250/4%20Tools/76mm%20Wide%20Dock/TPU/Split/) |

</details>

<details name="printers">
<summary style="cursor: pointer;">Voron 250mm Threaded 60mm Wide Dock</summary>

### Voron 250mm Threaded 60mm Wide Dock
| Tool Count | Left | Right | Center | Split |
|-|-|-|-|-|
| 2 |[](STL/Plates/Voron/250/2%20Tools/60mm%20Wide%20Dock/Threaded/Left/) |[](STL/Plates/Voron/250/2%20Tools/60mm%20Wide%20Dock/Threaded/Right/) |[](STL/Plates/Voron/250/2%20Tools/60mm%20Wide%20Dock/Threaded/Center/) |[](STL/Plates/Voron/250/2%20Tools/60mm%20Wide%20Dock/Threaded/Split/) |
| 3 | - | - |[](STL/Plates/Voron/250/3%20Tools/60mm%20Wide%20Dock/Threaded/Center/) |[](STL/Plates/Voron/250/3%20Tools/60mm%20Wide%20Dock/Threaded/Split/) |
| 4 | - | - |[](STL/Plates/Voron/250/4%20Tools/60mm%20Wide%20Dock/Threaded/Center/) |[](STL/Plates/Voron/250/4%20Tools/60mm%20Wide%20Dock/Threaded/Split/) |
| 5 | - | - | - |[](STL/Plates/Voron/250/5%20Tools/60mm%20Wide%20Dock/Threaded/Split/) |

</details>

<details name="printers">
<summary style="cursor: pointer;">Voron 250mm Threaded 76mm Wide Dock</summary>

### Voron 250mm Threaded 76mm Wide Dock
| Tool Count | Left | Right | Center | Split |
|-|-|-|-|-|
| 2 |[](STL/Plates/Voron/250/2%20Tools/76mm%20Wide%20Dock/Threaded/Left/) |[](STL/Plates/Voron/250/2%20Tools/76mm%20Wide%20Dock/Threaded/Right/) |[](STL/Plates/Voron/250/2%20Tools/76mm%20Wide%20Dock/Threaded/Center/) |[](STL/Plates/Voron/250/2%20Tools/76mm%20Wide%20Dock/Threaded/Split/) |
| 3 | - | - |[](STL/Plates/Voron/250/3%20Tools/76mm%20Wide%20Dock/Threaded/Center/) |[](STL/Plates/Voron/250/3%20Tools/76mm%20Wide%20Dock/Threaded/Split/) |
| 4 | - | - | - |[](STL/Plates/Voron/250/4%20Tools/76mm%20Wide%20Dock/Threaded/Split/) |

</details>

<details name="printers">
<summary style="cursor: pointer;">Voron 300mm TPU 60mm Wide Dock</summary>

### Voron 300mm TPU 60mm Wide Dock
| Tool Count | Left | Right | Center | Split |
|-|-|-|-|-|
| 2 |[](STL/Plates/Voron/300/2%20Tools/60mm%20Wide%20Dock/TPU/Left/) |[](STL/Plates/Voron/300/2%20Tools/60mm%20Wide%20Dock/TPU/Right/) |[](STL/Plates/Voron/300/2%20Tools/60mm%20Wide%20Dock/TPU/Center/) |[](STL/Plates/Voron/300/2%20Tools/60mm%20Wide%20Dock/TPU/Split/) |
| 3 |[](STL/Plates/Voron/300/3%20Tools/60mm%20Wide%20Dock/TPU/Left/) |[](STL/Plates/Voron/300/3%20Tools/60mm%20Wide%20Dock/TPU/Right/) |[](STL/Plates/Voron/300/3%20Tools/60mm%20Wide%20Dock/TPU/Center/) |[](STL/Plates/Voron/300/3%20Tools/60mm%20Wide%20Dock/TPU/Split/) |
| 4 | - | - |[](STL/Plates/Voron/300/4%20Tools/60mm%20Wide%20Dock/TPU/Center/) |[](STL/Plates/Voron/300/4%20Tools/60mm%20Wide%20Dock/TPU/Split/) |
| 5 | - | - |[](STL/Plates/Voron/300/5%20Tools/60mm%20Wide%20Dock/TPU/Center/) |[](STL/Plates/Voron/300/5%20Tools/60mm%20Wide%20Dock/TPU/Split/) |
| 6 | - | - | - |[](STL/Plates/Voron/300/6%20Tools/60mm%20Wide%20Dock/TPU/Split/) |

</details>

<details name="printers">
<summary style="cursor: pointer;">Voron 300mm TPU 76mm Wide Dock</summary>

### Voron 300mm TPU 76mm Wide Dock
| Tool Count | Left | Right | Center | Split |
|-|-|-|-|-|
| 2 |[](STL/Plates/Voron/300/2%20Tools/76mm%20Wide%20Dock/TPU/Left/) |[](STL/Plates/Voron/300/2%20Tools/76mm%20Wide%20Dock/TPU/Right/) |[](STL/Plates/Voron/300/2%20Tools/76mm%20Wide%20Dock/TPU/Center/) |[](STL/Plates/Voron/300/2%20Tools/76mm%20Wide%20Dock/TPU/Split/) |
| 3 | - | - |[](STL/Plates/Voron/300/3%20Tools/76mm%20Wide%20Dock/TPU/Center/) |[](STL/Plates/Voron/300/3%20Tools/76mm%20Wide%20Dock/TPU/Split/) |
| 4 | - | - | - |[](STL/Plates/Voron/300/4%20Tools/76mm%20Wide%20Dock/TPU/Split/) |

</details>

<details name="printers">
<summary style="cursor: pointer;">Voron 300mm Threaded 60mm Wide Dock</summary>

### Voron 300mm Threaded 60mm Wide Dock
| Tool Count | Left | Right | Center | Split |
|-|-|-|-|-|
| 2 |[](STL/Plates/Voron/300/2%20Tools/60mm%20Wide%20Dock/Threaded/Left/) |[](STL/Plates/Voron/300/2%20Tools/60mm%20Wide%20Dock/Threaded/Right/) |[](STL/Plates/Voron/300/2%20Tools/60mm%20Wide%20Dock/Threaded/Center/) |[](STL/Plates/Voron/300/2%20Tools/60mm%20Wide%20Dock/Threaded/Split/) |
| 3 |[](STL/Plates/Voron/300/3%20Tools/60mm%20Wide%20Dock/Threaded/Left/) |[](STL/Plates/Voron/300/3%20Tools/60mm%20Wide%20Dock/Threaded/Right/) |[](STL/Plates/Voron/300/3%20Tools/60mm%20Wide%20Dock/Threaded/Center/) |[](STL/Plates/Voron/300/3%20Tools/60mm%20Wide%20Dock/Threaded/Split/) |
| 4 | - | - |[](STL/Plates/Voron/300/4%20Tools/60mm%20Wide%20Dock/Threaded/Center/) |[](STL/Plates/Voron/300/4%20Tools/60mm%20Wide%20Dock/Threaded/Split/) |
| 5 | - | - |[](STL/Plates/Voron/300/5%20Tools/60mm%20Wide%20Dock/Threaded/Center/) |[](STL/Plates/Voron/300/5%20Tools/60mm%20Wide%20Dock/Threaded/Split/) |
| 6 | - | - | - |[](STL/Plates/Voron/300/6%20Tools/60mm%20Wide%20Dock/Threaded/Split/) |

</details>

<details name="printers">
<summary style="cursor: pointer;">Voron 300mm Threaded 76mm Wide Dock</summary>

### Voron 300mm Threaded 76mm Wide Dock
| Tool Count | Left | Right | Center | Split |
|-|-|-|-|-|
| 2 |[](STL/Plates/Voron/300/2%20Tools/76mm%20Wide%20Dock/Threaded/Left/) |[](STL/Plates/Voron/300/2%20Tools/76mm%20Wide%20Dock/Threaded/Right/) |[](STL/Plates/Voron/300/2%20Tools/76mm%20Wide%20Dock/Threaded/Center/) |[](STL/Plates/Voron/300/2%20Tools/76mm%20Wide%20Dock/Threaded/Split/) |
| 3 | - | - |[](STL/Plates/Voron/300/3%20Tools/76mm%20Wide%20Dock/Threaded/Center/) |[](STL/Plates/Voron/300/3%20Tools/76mm%20Wide%20Dock/Threaded/Split/) |
| 4 | - | - | - |[](STL/Plates/Voron/300/4%20Tools/76mm%20Wide%20Dock/Threaded/Split/) |

</details>

<details name="printers">
<summary style="cursor: pointer;">Voron 350mm TPU 60mm Wide Dock</summary>

### Voron 350mm TPU 60mm Wide Dock
| Tool Count | Left | Right | Center | Split |
|-|-|-|-|-|
| 2 |[](STL/Plates/Voron/350/2%20Tools/60mm%20Wide%20Dock/TPU/Left/) |[](STL/Plates/Voron/350/2%20Tools/60mm%20Wide%20Dock/TPU/Right/) |[](STL/Plates/Voron/350/2%20Tools/60mm%20Wide%20Dock/TPU/Center/) |[](STL/Plates/Voron/350/2%20Tools/60mm%20Wide%20Dock/TPU/Split/) |
| 3 |[](STL/Plates/Voron/350/3%20Tools/60mm%20Wide%20Dock/TPU/Left/) |[](STL/Plates/Voron/350/3%20Tools/60mm%20Wide%20Dock/TPU/Right/) |[](STL/Plates/Voron/350/3%20Tools/60mm%20Wide%20Dock/TPU/Center/) |[](STL/Plates/Voron/350/3%20Tools/60mm%20Wide%20Dock/TPU/Split/) |
| 4 | - | - |[](STL/Plates/Voron/350/4%20Tools/60mm%20Wide%20Dock/TPU/Center/) |[](STL/Plates/Voron/350/4%20Tools/60mm%20Wide%20Dock/TPU/Split/) |
| 5 | - | - |[](STL/Plates/Voron/350/5%20Tools/60mm%20Wide%20Dock/TPU/Center/) |[](STL/Plates/Voron/350/5%20Tools/60mm%20Wide%20Dock/TPU/Split/) |
| 6 | - | - | - |[](STL/Plates/Voron/350/6%20Tools/60mm%20Wide%20Dock/TPU/Split/) |

</details>

<details name="printers">
<summary style="cursor: pointer;">Voron 350mm TPU 76mm Wide Dock</summary>

### Voron 350mm TPU 76mm Wide Dock
| Tool Count | Left | Right | Center | Split |
|-|-|-|-|-|
| 2 |[](STL/Plates/Voron/350/2%20Tools/76mm%20Wide%20Dock/TPU/Left/) |[](STL/Plates/Voron/350/2%20Tools/76mm%20Wide%20Dock/TPU/Right/) |[](STL/Plates/Voron/350/2%20Tools/76mm%20Wide%20Dock/TPU/Center/) |[](STL/Plates/Voron/350/2%20Tools/76mm%20Wide%20Dock/TPU/Split/) |
| 3 | - | - |[](STL/Plates/Voron/350/3%20Tools/76mm%20Wide%20Dock/TPU/Center/) |[](STL/Plates/Voron/350/3%20Tools/76mm%20Wide%20Dock/TPU/Split/) |
| 4 | - | - |[](STL/Plates/Voron/350/4%20Tools/76mm%20Wide%20Dock/TPU/Center/) |[](STL/Plates/Voron/350/4%20Tools/76mm%20Wide%20Dock/TPU/Split/) |
| 5 | - | - | - |[](STL/Plates/Voron/350/5%20Tools/76mm%20Wide%20Dock/TPU/Split/) |

</details>

<details name="printers">
<summary style="cursor: pointer;">Voron 350mm Threaded 60mm Wide Dock</summary>

### Voron 350mm Threaded 60mm Wide Dock
| Tool Count | Left | Right | Center | Split |
|-|-|-|-|-|
| 2 |[](STL/Plates/Voron/350/2%20Tools/60mm%20Wide%20Dock/Threaded/Left/) |[](STL/Plates/Voron/350/2%20Tools/60mm%20Wide%20Dock/Threaded/Right/) |[](STL/Plates/Voron/350/2%20Tools/60mm%20Wide%20Dock/Threaded/Center/) |[](STL/Plates/Voron/350/2%20Tools/60mm%20Wide%20Dock/Threaded/Split/) |
| 3 |[](STL/Plates/Voron/350/3%20Tools/60mm%20Wide%20Dock/Threaded/Left/) |[](STL/Plates/Voron/350/3%20Tools/60mm%20Wide%20Dock/Threaded/Right/) |[](STL/Plates/Voron/350/3%20Tools/60mm%20Wide%20Dock/Threaded/Center/) |[](STL/Plates/Voron/350/3%20Tools/60mm%20Wide%20Dock/Threaded/Split/) |
| 4 | - | - |[](STL/Plates/Voron/350/4%20Tools/60mm%20Wide%20Dock/Threaded/Center/) |[](STL/Plates/Voron/350/4%20Tools/60mm%20Wide%20Dock/Threaded/Split/) |
| 5 | - | - |[](STL/Plates/Voron/350/5%20Tools/60mm%20Wide%20Dock/Threaded/Center/) |[](STL/Plates/Voron/350/5%20Tools/60mm%20Wide%20Dock/Threaded/Split/) |
| 6 | - | - | - |[](STL/Plates/Voron/350/6%20Tools/60mm%20Wide%20Dock/Threaded/Split/) |

</details>

<details name="printers">
<summary style="cursor: pointer;">Voron 350mm Threaded 76mm Wide Dock</summary>

### Voron 350mm Threaded 76mm Wide Dock
| Tool Count | Left | Right | Center | Split |
|-|-|-|-|-|
| 2 |[](STL/Plates/Voron/350/2%20Tools/76mm%20Wide%20Dock/Threaded/Left/) |[](STL/Plates/Voron/350/2%20Tools/76mm%20Wide%20Dock/Threaded/Right/) |[](STL/Plates/Voron/350/2%20Tools/76mm%20Wide%20Dock/Threaded/Center/) |[](STL/Plates/Voron/350/2%20Tools/76mm%20Wide%20Dock/Threaded/Split/) |
| 3 | - | - |[](STL/Plates/Voron/350/3%20Tools/76mm%20Wide%20Dock/Threaded/Center/) |[](STL/Plates/Voron/350/3%20Tools/76mm%20Wide%20Dock/Threaded/Split/) |
| 4 | - | - |[](STL/Plates/Voron/350/4%20Tools/76mm%20Wide%20Dock/Threaded/Center/) |[](STL/Plates/Voron/350/4%20Tools/76mm%20Wide%20Dock/Threaded/Split/) |
| 5 | - | - | - |[](STL/Plates/Voron/350/5%20Tools/76mm%20Wide%20Dock/Threaded/Split/) |

</details>

<details name="printers">
<summary style="cursor: pointer;">Micron 180mm TPU 60mm Wide Dock</summary>

### Micron 180mm TPU 60mm Wide Dock
| Tool Count | Left | Right | Center | Split |
|-|-|-|-|-|
| 2 |[](STL/Plates/Micron/180/2%20Tools/60mm%20Wide%20Dock/TPU/Left/) |[](STL/Plates/Micron/180/2%20Tools/60mm%20Wide%20Dock/TPU/Right/) |[](STL/Plates/Micron/180/2%20Tools/60mm%20Wide%20Dock/TPU/Center/) |[](STL/Plates/Micron/180/2%20Tools/60mm%20Wide%20Dock/TPU/Split/) |
| 3 | - | - |[](STL/Plates/Micron/180/3%20Tools/60mm%20Wide%20Dock/TPU/Center/) |[](STL/Plates/Micron/180/3%20Tools/60mm%20Wide%20Dock/TPU/Split/) |
| 4 | - | - | - |[](STL/Plates/Micron/180/4%20Tools/60mm%20Wide%20Dock/TPU/Split/) |

</details>

### Umbilical Plate Installation
If you have one, install the logo insert. The insert is indexed with a couple tabs which need to be inserted first. The bottom will press fit in to place.
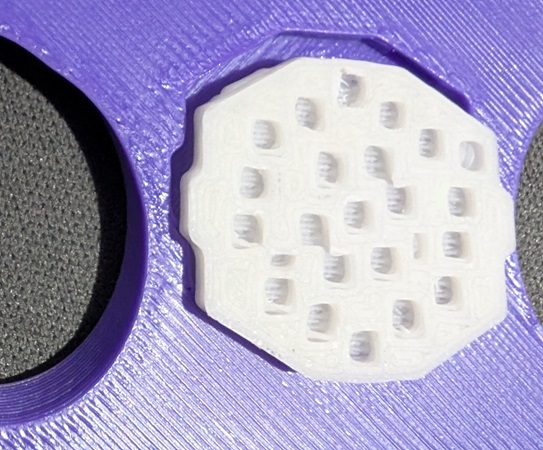
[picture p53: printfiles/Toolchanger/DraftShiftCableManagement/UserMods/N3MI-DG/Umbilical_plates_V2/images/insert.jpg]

The Voron face plate requires 4 heatset inserts to be installed.
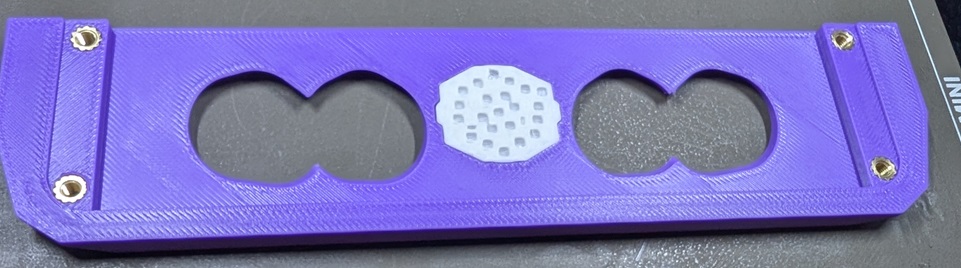
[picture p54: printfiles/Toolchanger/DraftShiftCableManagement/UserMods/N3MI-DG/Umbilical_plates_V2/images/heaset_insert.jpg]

Optionally you can add some foam to the mating surface of the face place.

If you have a SC Barf LED, press fit it in to the outer plate.

Mate the face plate and outer plate together by putting the face plate over one side of the ports and flexing it over the other. It may feel like the pieces don't fit at first, but with a bit of flex and force the face plate will go over all of the ports.

Install the plates on to the back panel of the printer. You need to have the panel removed from the frame or at least undo the top clips so that it can be installed from the outside of the printer.

For the Voron version, secure the back plate to the frame with 2 M5x10 BHCS screws and the outer plate to the face plate with 4 M3x8 SHCS screws.

The Micron version gets secured to the frame with 2 M3x10 SHCS and the outer plate to the face plate with 2 M2x10 self tapping screws.

If you are using the threaded back plates the spring steel/piano wire can be secured to the back plate with a M3 heat insert, M3x6 BHCS and M3 washer.

___
## Umbilical Restraints
There are 2 different ports for the umbilical plates.
- TPU - Uses a TPU printed cable relief.
- THREADED - Uses either M12x1.5 or PG7 cable glands.

There are 2 supported methods of taming the umbilical.
- Flat Spring Steel - 0.3x3mm (preferred) [Link](https://www.aliexpress.com/item/1005006731615186.html "Aliexpress")
- Piano Wire - 1mm

### TPU STL Files
To download the TPU restraint STL files select one of the links below.
###### Spring Steel
- [Voron 3.7mm cable](STL/TPU%20Umbilical/Voron/Spring/3.7mm%20Cable)
- [Voron 4mm cable](STL/TPU%20Umbilical/Voron/Spring/4mm%20Cable)
- [Voron 4.5mm cable](STL/TPU%20Umbilical/Voron/Spring/4.5mm%20Cable)
- [Voron 5mm cable](STL/TPU%20Umbilical/Voron/Spring/5mm%20Cable)
- [Voron 5.5mm cable](STL/TPU%20Umbilical/Voron/Spring/5.5mm%20Cable)
- [Voron 6mm cable](STL/TPU%20Umbilical/Voron/Spring/6mm%20Cable)
- [Voron 6.35mm cable](STL/TPU%20Umbilical/Voron/Spring/6.35mm%20Cable)
- [Micron 3.7mm cable](STL/TPU%20Umbilical/Micron/Spring/3.7mm%20Cable)
- [Micron 4mm cable](STL/TPU%20Umbilical/Micron/Spring/4mm%20Cable)
- [Micron 4.5mm cable](STL/TPU%20Umbilical/Micron/Spring/4.5mm%20Cable)
- [Micron 5mm cable](STL/TPU%20Umbilical/Micron/Spring/5mm%20Cable)
- [Micron 5.5mm cable](STL/TPU%20Umbilical/Micron/Spring/5.5mm%20Cable)
- [Micron 6mm cable](STL/TPU%20Umbilical/Micron/Spring/6mm%20Cable)
- [Micron 6.35mm cable](STL/TPU%20Umbilical/Micron/Spring/6.35mm%20Cable)
###### Piano Wire
- [Voron 3.7mm cable](STL/TPU%20Umbilical/Voron/Wire/3.7mm%20Cable)
- [Voron 4mm cable](STL/TPU%20Umbilical/Voron/Wire/4mm%20Cable)
- [Voron 4.5mm cable](STL/TPU%20Umbilical/Voron/Wire/4.5mm%20Cable)
- [Voron 5mm cable](STL/TPU%20Umbilical/Voron/Wire/5mm%20Cable)
- [Voron 5.5mm cable](STL/TPU%20Umbilical/Voron/Wire/5.5mm%20Cable)
- [Voron 6mm cable](STL/TPU%20Umbilical/Voron/Wire/6mm%20Cable)
- [Voron 6.35mm cable](STL/TPU%20Umbilical/Voron/Wire/6.35mm%20Cable)
- [Micron 3.7mm cable](STL/TPU%20Umbilical/Micron/Wire/3.7mm%20Cable)
- [Micron 4mm cable](STL/TPU%20Umbilical/Micron/Wire/4mm%20Cable)
- [Micron 4.5mm cable](STL/TPU%20Umbilical/Micron/Wire/4.5mm%20Cable)
- [Micron 5mm cable](STL/TPU%20Umbilical/Micron/Wire/5mm%20Cable)
- [Micron 5.5mm cable](STL/TPU%20Umbilical/Micron/Wire/5.5mm%20Cable)
- [Micron 6mm cable](STL/TPU%20Umbilical/Micron/Wire/6mm%20Cable)
- [Micron 6.35mm cable](STL/TPU%20Umbilical/Micron/Wire/6.35mm%20Cable)

 Optionally, there is also a TPU plug to block the ports if you do not have all of your tools built. [Link](STL/TPU%20Umbilical/Relief_Plug.stl, "TPU Plug")
### Installation
You need to print 1 Relief, 1 Terminator and enough Clips to keep your umbilical tidy (typically 4-6) per tool.
The spring steel/piano wire length should be the diagonal length of your bed + enough material for bending (~25mm). This is a good starting point for Voron printers.
#### Spring Steel
Spring steel can snap rather easily when bending. Before bending heat the area with a blow torch or lighter to a cherry red and let it cool. This makes the steel more ductile and will bend without snapping.
If there is too much friction while feeding the spring steel you can add a dab of dish washing liquid as a lubricant.
<br/>Insert the spring steel through the strain relief and out the back. Bend it 180 degrees 12mm from the end.
 
<br/>Do a second bend at ~60 degrees 6mm from the end that was bent in the previous step.
 
<br/>
<br/>Feed the spring steel through all of the clips matching the hole orientation to the strain relief.<br/>
<br/>Feed the spring steel through the terminator and do 2 bends at ~30 degrees. Feed the spring steel back until the bend is inside the slot for the spring steel.<br/> 
<br/>Mount the bowden tube and cable in the strain relief and inset the strain relief into the plate. This is the time to determine the length you need. With the strain relief inserted in the back plate, run your cable to the tool while it is at the largest travel position for that specific tool. For instance, T0 would be at MAX_X and MIN_Y, The last tool would be at MIN_X and MIN_Y. Make sure that at that position there is minimal slack, but there should be some. You do not want the umbilical to be putting strain on the toolhead. Then work your way back from the toolhead and insert the bowden tube and cable into the termination print, and then the clips (which can be spaced evenly). If at any point there is too little or too much slack, pull out the strain relief and adjust it.

<br/>Optionally you can add some heat shrink (with glue) to keep the clips from moving.<br/>
#### Piano Wire
The procedure for piano wire is much the same as spring steel except the wire gets 2 90 degree bends at the Relief and Terminator.



___
# Credits
Developed by [N3MI-DG](https://github.com/N3MI-DG)
- [viesturz](https://github.com/viesturz) for the Tapchanger TPU umbilicals, which were the inspiration for this system.
- [hartk1213](https://github.com/hartk1213) as the umbilical plate aesthetics were recreated based on his Micron R1 exhaust plate.

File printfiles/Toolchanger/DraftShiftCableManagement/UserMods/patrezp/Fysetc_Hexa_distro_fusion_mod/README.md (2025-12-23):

# Fysetc Hexa distro fusion holder for StealthChanger



I had to widen (by 22.5mm to each side) the existing base, cover, PTFE ramps and cover ramp for n3mi's umbilical plates, as this board is really big and it could not fit the existing FannyPack. Added 1cm on top of the base to add more clearance to USB cables.

## BOM
4x voron heatset inserts

Rest of stuff needed to build FannyPack

Optional: 90° USB-C cable or adapter, as it is really tough with some cables to bend them

### Credits
[DraftShift Design] (https://github.com/DraftShift) for the original FannyPack

[Fysetc] (https://github.com/FYSETC/Hexa_Distro_Fusion) for releasing the drawings for the board

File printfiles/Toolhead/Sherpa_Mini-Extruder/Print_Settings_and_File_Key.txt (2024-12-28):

Primary Color: nothing at start of file name
Accent Color: [a]_ at start of file name
Quantity Required: _x# near end of file name
File Revision: _Rev# at end of file name

Nozzle Size: 0.4mm (RECOMMENDED)
Recommended FDM Materials: ASA (Fillamentum, Prusament, Polymaker or 3DXTech Recommended)
Alternate Approved FDM Materials: PC (3DXTech Recommended)
Layer Height: 0.10mm or 0.2mm
Extrusion Width: Forced 0.4mm
Infill Percentage: 40% minimum (at 0.6mm Width)
Infill Type: Grid, Gyroid, Honeycomb, Triangle or Cubic
Wall Count: 4 minimum (at 0.4mm Width)
Solid Top/Bottom Layers: 5 minimum (at 0.2mm Height)

Nozzle Size: 0.5mm 
Recommended FDM Materials: ASA (Fillamentum, Prusament, Polymaker or 3DXTech Recommended)
Alternate Approved FDM Materials: PC (3DXTech Recommended)
Layer Height: 0.1 or 0.2mm
Extrusion Width: Forced 0.5mm
Infill Percentage: 40% minimum (at 0.6mm Width)
Infill Type: Grid, Gyroid, Honeycomb, Triangle or Cubic
Wall Count: 4 minimum (at 0.5mm Width)
Solid Top/Bottom Layers: 5 minimum (at 0.2mm Height)

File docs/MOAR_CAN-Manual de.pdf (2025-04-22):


# MOAR_CAN

# Handbuch

MOAR_CAN ist ein CAN-Bus-Hub, der für IDEX-Drucker, Werkzeugwechsler und andere 3D-Druckeranwendungen entwickelt wurde, bei denen mehrere CAN-Geräte miteinander verbunden werden müssen. Im Gegensatz zu den meisten 3D-Drucker-CAN-Bus-Hubs auf dem Markt ist MOAR_CAN so konzipiert, dass er einer linearen Bustopologie mit kurzen Stub-Längen folgt. Der 1Mbit-CAN-Bus-Standard (ISO 11898) empfiehlt eine maximale Buslänge von 40 Metern, mit maximal 30 Knoten (CAN-Geräten) und einer maximalen Stichleitungslänge von 300mm, mit 120-Ohm-Abschlusswiderständen an beiden Enden des Busses.
Die meisten auf dem Markt befindlichen CAN-Bus-Hub-Platinen sind aufgebaut:


Wie Sie oben sehen können, ist der lineare CAN-Bus sehr kurz (die Länge der Leiterbahn auf der Platine + die Länge der Drähte vom USB- zum CAN-Adapter), und die Werkzeugkopfstecker auf den Platinen wirken wie Stichleitungen. Wie bereits erwähnt, beträgt die maximal empfohlene Stichleitungslänge 300 mm, aber die Kabelführung zum Toolhead ist wahrscheinlich viel länger als das. Das bedeutet, dass diese CAN-Hub-Platinen zwar funktionieren können, aber nicht der empfohlenen Topologie entsprechen, was bedeutet, dass CAN-Bus-bezogene Probleme wie Kommunikationsfehler wahrscheinlicher sind.
Dieses Design hält den linearen CAN-Bus kurz, aber eine Buslänge von bis zu 40 Metern liegt innerhalb der empfohlenen Spezifikationen, so dass dies keinen großen Unterschied machen sollte.
MOAR_CAN wurde entwickelt, um die Länge der Stichleitung so kurz wie möglich zu halten, und erfordert einen längeren Bus, um die empfohlenen Spezifikationen so genau wie möglich einzuhalten. Dies erfordert, dass der CAN-Bus zum Toolhead (oder einem anderen CAN-Gerät) geht und von dort wieder zurückkommt.

MOAR_CAN ist konzipiert:


(In dieser Zeichnung hat der Knoten 6 keinen Abschlusswiderstand und ist am Hub abgeschlossen, aber der Abschluss kann auch am Knoten sein).
Bei diesem Design gehen die Busdrähte zu den Knoten und kommen wieder zurück, wobei der Hub nur die Drähte, die von einem Knoten kommen, mit den Drähten verbindet, die zum nächsten Knoten gehen. Am CAN-Knoten (z. B. auf der Werkzeugkopfplatine) werden die beiden CAN-Drahtpaare am CAN-Anschluss miteinander verbunden, so dass es sich um einen langen linearen Bus handelt. Die Stichleitungslänge ist der Abstand der Drähte (meist Leiterbahnen auf der Leiterplatte) zwischen dem Anschluss und dem CAN-Transceiver auf der Leiterplatte, normalerweise im niedrigen zweistelligen Millimeterbereich.
Beide verdrillten Paare können im selben Kabel sein. Auf der Nabenseite verwenden Sie einen 6-poligen MX3.0 2x3-Stecker und auf der Geräteseite einen 4-poligen Stecker, wie MX3.0 2x2 oder XT30(2+2). Die 2 Drähte für CAN H und L werden mit demselben Crimpstift verbunden.
Das bedeutet natürlich, dass Sie mehr Drähte zu Ihren CAN-Geräten verlegen müssen. Es gibt einige 6-adrige Leitungen mit 2 dicken Leitern (für die Stromversorgung) und 2 Paaren dünner verdrillter Adern (die Ein- und Ausgangs-CAN-Leitungen) auf dem Markt, wie z.B. IGUS Chainflex CF113-018-D. Diese Leitungen sind in der Regel für Servomotoren in industriellen Anwendungen konzipiert, eignen sich aber auch für diesen Anwendungsfall.
Das oben erwähnte IGUS-Kabel kann von Isik's Tech hier erworben werden: [TBD]

Dies ist die Pinbelegung des 6-poligen MX3.0-Anschlusses am MOAR_CAN:


Wie Sie sehen können, sind die äußeren Pins für den CAN-Bus. Ein Paar von Drähten sollte von einer Seite des Anschlusses am MOAR_CAN zum Anschluss am CAN-Gerät verlaufen. Am Anschluss des CAN-Geräts sollte das andere Paar CAN-Drähte mit den CAN-Drähten verbunden werden, die vom MOAR_CAN ausgehen, und sie sollten zur anderen Seite des Anschlusses am MOAR_CAN zurückführen.
Wenn kein 6-poliger Stecker verwendet werden soll, müssen die Stiftleisten dahinter mit Steckbrücken versehen werden. Diese Steckbrücken verbinden die CAN-Pins auf beiden Seiten des Steckers miteinander.


Die CAN-Drähte von Ihrem USB/CAN-Adapter (PiCAN, ToqueCAN usw.) können
mit dem MOAR_CAN über den XH2.54-MOAR_CAN-Stecker oder den MX3.0-2x2-Stecker verbunden (mehr über diesen Stecker später).
Der MOAR_CAN Stecker hat Pins für beide Enden des CAN-Busses am MOAR_CAN. Dies gewährleistet die Kompatibilität mit ToqueCANs. Für Nicht-ToqueCAN-Anwendungen sollte das innere Paar der Pins verwendet werden. Für ToqueCANs sollten Sie alle 4 Pins verwenden und sicherstellen, dass die Pinbelegung an beiden Enden des Kabels gleich ist. Jedes CAN-Drahtpaar sollte verdrillt sein.
Pinbelegung des MOAR_CAN-Steckers:


Auf der Platine befindet sich auch ein 120-Ohm-CAN-Abschluss-Jumper. Dieser sollte nicht bestückt werden, wenn der MOAR_CAN mit einem ToqueCAN verwendet wird. Er sollte auch nicht bestückt werden, wenn das letzte an das MOAR_CAN angeschlossene CAN-Gerät terminiert ist. Wenn das letzte an das MOAR_CAN angeschlossene CAN-Gerät nicht über die 120-Ohm-CAN-Terminierung verfügt, sollte ein Jumper angeschlossen werden, damit der CAN-Bus an beiden Enden des Busses terminiert ist.
Ihr USB/CAN-Adapter sollte ebenfalls terminiert sein, außer bei Verwendung eines ToqueCAN. Bei einem ToqueCAN sollten die 2 CAN-Geräte, die mit dem ToqueCAN verbunden sind, terminiert werden.
120-Ohm-Abschluss-Steckbrücke:


Dies ist die Pinbelegung des 4-poligen MX3.0-Anschlusses am MOAR_CAN:


Bitte achten Sie auf diese Belegung und überprüfen Sie, ob Ihr Kabel die gleiche Belegung hat, da diese nicht mit der des ToqueCAN oder anderer CAN-Geräte mit dem gleichen Stecker übereinstimmt.
Dieser Anschluss kann für verschiedene Anwendungsfälle genutzt werden.
Sie können diesen Anschluss als CAN-Bus-Eingang anstelle des XH2.54-Anschlusses verwenden, wenn Sie einen USB/CAN-Adapter verwenden, der nicht von ToqueCAN stammt. Sie können ihn in diesem Fall auch für die Stromversorgung der Platine verwenden, aber beachten Sie bitte, dass die maximale Stromstärke des MX3.0-Anschlusses 10,5A beträgt, oder etwa 250W, wenn Sie ein 24V-System verwenden. Verwenden Sie diesen Anschluss nicht für die Stromversorgung, wenn Sie den MOAR_CAN zur Versorgung von Geräten verwenden wollen, die mehr Strom verbrauchen, wie z.B. mehrere Werkzeugkopfplatinen.
Wenn Sie einen Nicht-ToqueCAN-USB/CAN-Adapter verwenden und den MOAR_CAN-Anschluss wie auf der vorherigen Seite beschrieben nutzen, können Sie diesen Anschluss für ein zusätzliches CAN-Gerät verwenden, wenn die Bolzenlänge (Kabellänge) kurz genug ist. Bis zu 250mm sollten in Ordnung sein.
Wenn Sie einen USB/CAN-Adapter verwenden, der nicht von ToqueCAN stammt, und diesen Anschluss für ein CAN-Gerät verwenden möchten, aber ein längeres Kabel als 250
mm zum CAN-Gerät benötigen, können Sie stattdessen die äußeren Pins des MOAR_CAN-Anschlusses verwenden. In diesem Fall muss das CAN-Gerät einen 120-Ohm-Abschluss haben, und der 120-Ohm-Abschluss am MOAR_CAN kann nicht verwendet werden. Ihr USB/CAN-Adapter benötigt ebenfalls die 120-Ohm-Terminierung, und kein anderes an das MOAR_CAN angeschlossenes CAN-Gerät kann die 120-Ohm-Terminierung haben.

Dies ist die Pinbelegung der Schraubklemmleiste:


Dieser Anschluss ist für den Stromeingang. Der maximale Gesamtstrom, den das MOAR_CAN an alle angeschlossenen Geräte liefern kann, beträgt 24 A, und der maximale Strom, den das MOAR_CAN an ein angeschlossenes Gerät liefern kann, beträgt 10,5 A. Bitte verwenden Sie das MOAR_CAN nicht, um mehr Strom als diese Werte zu liefern.
●

### xbst_ - Isiks Technik

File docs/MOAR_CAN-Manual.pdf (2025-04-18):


# MOAR_CAN

# Manual

MOAR_CAN is a CAN bus hub designed for IDEX printers, toolchangers and other 3D printer applications where multiple CAN devices need to be connected together. Unlike most 3D printer CAN bus hubs on the market, MOAR_CAN is designed to follow a linear bus topology with short stub lengths. 1Mbit CAN bus standard (ISO 11898) recommends a maximum bus length of 40 meters, with a maximum of 30 nodes (CAN devices) and a maximum stub length of 300mm, with 120-ohm termination resistors on both ends of the bus.
Most CAN bus hub PCBs on the market are designed like this:


As you can see above, the linear CAN bus is very short (the trace length on the PCB + the length of the wires from the USB to CAN adapter), and the toolhead connectors on the PCBs act like stubs. As stated earlier, the maximum recommended stub length is 300mm, but the cable run to the toolhead is likely much longer than that. This means, while these CAN hub PCBs may work, they don’t follow the recommended topology, meaning CAN bus-related problems like communication errors are more likely to happen.
This design keeps the linear CAN bus short, but up to 40 meters of bus length is within the recommended specs, so this should not make a big difference. MOAR_CAN is designed to keep the stub length as short as possible, and requires a longer bus to follow the recommended specs as closely as possible. This requires the CAN bus to go to the toolhead (or other CAN device) and come back from there.

MOAR_CAN is designed like this:


(In this drawing, node 6 doesn't have the termination resistor and it’s terminated on the hub, but the termination can be on the node as well.) With this design, the bus wires go to the nodes, and come back, with the hub just joining the wires coming from one node with the wires going to the next node. On the CAN node (like toolhead PCB), the 2 pairs of CAN wires are joined together on the CAN connector, effectively making it a long linear bus. The stub length ends up being the distance of wires (mostly PCB traces) between the connector and the CAN transceiver on the PCB, usually low double-digit millimeters.
Both twisted pairs can be in the same cable. On the hub end, you use a 6-pin MX3.0 2x3 connector, and on the device end, you use a 4-pin connector, like MX3.0 2x2 or XT30(2+2). The 2 wires for CAN H and L get joined in the same crimp pin.
This, of course, means that you need to run more wires to your CAN devices. There are some 6 wire cables with 2 thick conductors (for power) and 2 pairs of thinner twisted wires (the in and out CAN wires) on the market, like IGUS Chainflex CF113-018-D. These cables are usually designed for servo motors in industrial applications, but they are also suitable for this use case.
The IGUS cable mentioned above can be purchased from Isik’s Tech here: [TBD]

This is the pinout of the 6-pin MX3.0 connector on the MOAR_CAN:


As you can see, the outer pins are for the CAN bus. A pair of wires should run from 1 side of the connector on the MOAR_CAN to the connector on the CAN device. On the connector on the CAN device, the other pair of CAN wires should be joined to the CAN wires running from the MOAR_CAN, and they should run back to the other side of the connector on the MOAR_CAN.
If a 6-pin connector is not going to be used, the pin headers behind it needs to have jumpers populated. These jumpers connect the CAN pins on both sides of the connector together.


The CAN wires from your USB/CAN adapter (PiCAN, ToqueCAN, etc.) can be connected to the MOAR_CAN using the XH2.54 MOAR_CAN connector, or the MX3.0 2x2 connector (more about this connector later).
The MOAR_CAN connector has pins for both ends of the CAN bus on the MOAR_CAN. This ensures compatibility with ToqueCANs. For non-ToqueCAN applications, the inner pair of pins should be used. For ToqueCANs, use all 4 pins, and make sure the pinouts on both ends of the cable are the same. Each pair of CAN wires should be twisted.
MOAR_CAN connector pinout:


There is a 120-Ohm CAN termination jumper on the PCB as well. This should not be populated if using the MOAR_CAN with a ToqueCAN. It should not be populated if the last CAN device connected to the MOAR_CAN is terminated either. If the last CAN device connected to the MOAR_CAN does not have the 120-Ohm CAN termination, then a jumper should be connected, so the CAN bus has termination on both ends of the bus.
Your USB/CAN adapter should also be terminated, except when using a ToqueCAN. With a ToqueCAN, the 2 CAN devices connected to the ToqueCAN should be terminated.
120-Ohm Termination Jumper:


This is the pinout of the 4-pin MX3.0 connector on the MOAR_CAN:


Please pay attention to this pinout and double check if your cable has the same pinout, as this is not the same as the ToqueCAN or other CAN devices with the same connector.
This connector can be used for a few different use cases.
You can use this connector as the CAN bus in connector instead of the XH2.54 connector if you are using a non-ToqueCAN USB/CAN adapter. You can also use it to supply power to the PCB in this case, but please keep in mind the maximum current the MX3.0 connector is rated for is 10.5A, or about 250W if you are using a 24V system. Do not use this connector for power if you are going to use the MOAR_CAN to deliver power to devices consuming more power than this, like multiple toolhead PCBs.
If you are using a non-ToqueCAN USB/CAN adapter, and use the MOAR_CAN connector as described in the previous page, you can use this connector for an auxiliary CAN device, if the stud length (cable length) is short enough. Up to 250mm should be ok.
If you are using a non-ToqueCAN USB/CAN adapter, and you want to use this connector for a CAN device, but you need a longer-than-250mm cable going to the CAN device, you can use the outer pins of the MOAR_CAN connector instead. In this case, this CAN device needs to have the 120-Ohm termination, and the 120-Ohm termination on the MOAR_CAN cannot be used. Your USB/CAN adapter also needs the 120-Ohm termination, and no other CAN device connected to the MOAR_CAN can have the 120-Ohm termination.

This is the pinout of the screw terminal block:


This connector is for the power input. The maximum total current the MOAR_CAN can supply to all devices connected to it is 24A, and the maximum current the MOAR_CAN can supply to a device connected to it is 10.5A. Please do not use the MOAR_CAN to deliver more power than these ratings.

### xbst_ - Isik’s Tech

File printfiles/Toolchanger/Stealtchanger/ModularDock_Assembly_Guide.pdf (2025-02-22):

# DRAFTSHIFT DESIGN

VERSION 2024-04-12

MODULAR DOCK V1 BUILD GUIDE

Because you need a safe place to store all

the tools you’ve built.

## PREFACE

Before you begin on your journey, a word of caution.

In the comfort of your own home you are about to assemble a robot. This machine can maim, burn, and electrocute you if you are not careful. Please do not become the first STEALTHCHANGER fatality. There is no special Reddit flair for that.

Please, read the entire manual before you start assembly. As you begin wrenching, please check our Discord channels for any tips and questions that may halt your progress.

Most of all, good luck!

THE DRAFTSHIFT DESIGN TEAM

2

## GITHUB.COM/DRAFTSHIFT/MODULARDOCK

## TABLE OF CONTENTS

Introduction | 04
Hardware | 07
Frame | 08
Base | 10
Back Plate | 12
Wipers | 13
Install | 15
Containers | 17
Setup Tool | 18
Next Steps | 19

3

## INTRODUCTION

PART PRINTING GUIDELINES

The Voron Team has provided the following print guidelines for you to follow in order to have the best chance at success with your parts. The StealthChanger Team recommends to follow the same standards. There are often questions about substituting materials or changing printing standards, but we recommend you follow these:

3D PRINTING PROCESS
Fused Deposition Modelling (FDM)

MATERIAL
ABS

LAYER HEIGHT
Recommended: 0.2mm

EXTRUSION WIDTH
Recommended: Forced 0.4mm

INFILL TYPE
Grid, Gyroid, Honeycomb, Triangle or Cubic

INFILL PERCENTAGE
Recommended: 40%

WALL COUNT
Recommended: 4

SOLID TOP/BOTTOM LAYERS
Recommended: 5

4

## INTRODUCTION

FILE NAMING

By this time you should have already downloaded our STL files from the StealthChanger GitHub. You might have noticed that we have used the Voron naming convention for the files. This is how to use them.

PRIMARY COLOUR

Example part_x4.stl

These files will have nothing at the start of the filename.

ACCENT COLOUR

Example [a]_part.stl

We have added “[a]” to the front of any STL file that is intended to be printed with accent colour.

QUANTITY REQUIRED

Example [a]_part_x4.stl

If any file ends with “_x#”, that is telling you the quantity of that part required to build the machine.

HOW TO GET HELP

If you need assistance with your build, we are here to help. Head on over to our Discord group and post your questions. This is our primary medium to help STEALTHCHANGER Users and we have a great community that can help you out if you get stuck.

5

### https://discord.gg/jJs73c6vSc

## INTRODUCTION

REPORTING ISSUES

Should you find an issue in the documentation or have a suggestion for an improvement please consider opening an issue on GitHub (https://github.com/DraftShift/ModularDock/issues). When raising an issue please include the relevant page numbers and a short description; annotated screenshots are also very welcome. We periodically update the manual based on the feedback we get.

THIS IS JUST A REFERENCE

This manual is designed to be a simple reference manual. Building a StealthChanger can be a complex endeavour and for that reason we recommend downloading the CAD files off our Github repository if there are sections you need clarification on. It can be sometimes be easier to follow along when you have the whole assembly in front of you.

### https://github.com/DraftShift/ModularDock

6

## HARDWARE REFERENCE

BUTTON HEAD CAP SCREW (BHCS) Metric fastener with a domed shape head and hex drive. Most commonly found in locations where M5 fasteners are used. ISO 7380-1 | SOCKET HEAD CAP SCREW (SHCS) Metric fastener with a cylindrical head and hex drive. The most common fastener used on the Voron. ISO 4762
FLAT HEAD COUNTERSUNK SCREW (FHCS) Metric fastener with a cone shaped head and a flat top. ISO 10642 | HEAT SET INSERT Heat inserts with a soldering tip so that they melt the plastic when installed. As the plastic cools, it solidifies around the knurls and ridges on the insert for excellent resistance to both torque and pull-out.
MAGNET Metric round button neodymium magnet. | SPRING Small stiff spring, be prepared to cut to fit.
HIGH TEMP RTV SILICON High Temp RTV Silicon in a tube for making moulds, make sure it can handle the temp of the nozzle. | T-NUT A type of nut that slides into the extrusion rail as a method of affix other parts to it.

HEX NUT Metric hex nut used with metric fasteners.

7

## FRAME

8


## Heat Set

INSERT HEAT SETS

Start by setting the heat sets.

PARTS

The parts required to build a frame, Top, Bottom, Left and Right.


OPTIONAL INSERT HEAT SETS

Optionally add these inserts when using the “L Bracket”, recommended if top mounting.

## FRAME


ASSEMBLE

Use M3x16mm socket head screws to attach the top and bottom to the frame sides. Make sure to get them straight and tight.

## M3x16mm SHCS

9


BASES


The modular dock has lots of options. This is to support different types of tools as well as a variety of nozzle blockers and wipers when at rest. Since the assembly is all the same we will only show the stealthburner. But rest assured they all use the same hardware and process.

NOTE: stubby version can not be used with extended front frame, 2020 front frame only.

NOTE: stubby version can not be used with any other tools, so if you choose the stubby version you can only use dragonburners and stubby docks. Also the bolts are slightly shorter see the BOM.

## BASE

10

Stealthburner | Dragonburner | Blackbird

## BASE


INSERT HEAT SETS

Start by setting the heat sets.

ATTACHING TO FRAME

Insert the bolts from the front of the dock and snug them. Then install the longer bolts via the back of the base and tighten. Then return to the front and tighten.

NOTE: 40mm screws are used in place of the 50mm for the stubby version.

## Heat Set

11

M3x50mm SHCS

## M3x20mm SHCS

## BACK PLATE

12

Heat Set

OPTIONAL HEAT SET

Optional heat set for PTFE wiper install.

NOTE: There are 2 optional 6x3 magnets on the bottom for future options to attach to.


## M3x10mm SHCS

INSTALL BACK PLATE

Screw the back plate on, just snugging it up as we will adjust this later in the manual.

13

## WIPERS

WIPERS

Just like bases, wipers have options. The main ones are Cup or Spring Steel version. Both were designed by TapChanger and adopted for these docks.

INSERT HEAT SETS; Start by setting the heat sets.; Heat Set; Spring Steel

## Cup Style

M3x6mm BHCS | M3x16mm BHCS + M4 Spring
Spring Steel | Cup Style

INSTALL BLOCKER

Both types will require High Temp RTV Silicon moulds.

CUP: Install the heat set from the bottom of the cup, install an M3 screw from the bottom to be flush, then fill the cup with silicon and with a wet finger press it smooth and let it dry then install, cut the spring to be about 2-3mm high.

SPRING STEEL: Use the provided mould, fill both sides with silicon, insert the spring steel and close the mould. Let dry and install.

14

## WIPERS

M3x30mm SHCS; INSTALL WIPER; installed.

OPTIONAL PTFE WIPER

Cut a 8mm piece of 4mm OD PTFE tube. Fit between the 2 holes and screw in an M2.5x6mm (2mm ID) or M3x6mm FHCS (3mm ID) screw to each end to hold the PTFE tube in place.

Install the assembled wiper onto the back plate.

Install the wiper into the base of the dock. Seen here with the back plate already

NOTE: 20mm screws used for DB width docks.


## M3x6mm BHCS

## 6mm FHCS + 8mm PTFE Tube

## MOUNTING

L BRACKET

Once you have the docks mounted to the top bar, add 2 more M5 T-Nuts to the inside of the top rail. Using M5 BHCS to the rail and M3 BHCS to the attach the bracket to the dock.

MOUNTING OPTIONS

Like most parts of the modular dock, you have options at this point.

- Top mount, this meant only mounting to the top bar of the frame. In this configuration, you should use the “L Bracket” and the bottom “Links”.
- Bottom mount or Crossbar Mount, this means you are only mounting to a bar that runs in parallel to the top frame bar, but at least 170mm lower. In this configuration nothing is mounted to the top and no extras are required.
- Full mount, this means you are running both top and bottom bars to mount to. This is the most solid option and the most solid by far. You do not need any extra brackets.

The guide will go over all the options, but you will not need all options.

Extrusion mounts require 2x M5 T-Nuts and 2x M5x10mm BHCS per rail. Since this is self explanatory we won’t show images of these options.

15


## M3x8mm BHCS

## M5x10mm BHCS

## M5 T-Nut

CORNER BRACKETS

These are a good idea either way, but specifically if top mounting it is highly recommended to add corner brackets on the top rail. The leverage of the docks will allow the rail to spin on the blind join, this will counter it.

## MOUNTING

M5x10mm BHCS; M5 Nut

LINKS

Each dock will require 2 links. There are lots of combinations, the end piece has a single hole in it and is meant to start or end a chain of docks. Between docks there are different lengths, this is do to the size of and proper spacing between the tools/docks. The links are names to match the toolhead combinations to maintain the proper gap.

NOTE: Blackbird (BB) is the same length as SB.

NOTE: Links are strongly recommended as they add lots of stiffness across docks when no crossbar is available.

16

M3x20mm SHCS

BUFFER BRACKET

This is a special bracket to help secure the top part of the dock when used with the door buffer. It uses the L Bracket heat sets and screws into the printer top rail.

## CONTAINERS

OPTIONAL CONTAINER

Each dock can hold one optional container. There are several types and each type simply clips in. The container have the male side and the dock frame has the dimples at the top where they click into.

The blank version is provided for you to build off of it or if you want to add a tool ID to it. The grill version adds nice Voron style hexes to the top. The fancier version allow for electronics, there is a 3mm diameter wire path near the top of the frames to be able to safely run power to the top rail and across the docks.


17

BLANK

GRILL

KNOMI


KNOMI V2

## SETUP TOOL


SETTING UP THE TOOL

There are 2 steps to this.

1. This step we want to make sure the tool sits at a perfect 90 degrees. Sit the tool into the dock and adjust the back plate (slotted bolts) until the dock can hold the tool at a perfect 90 degrees on it’s own. Make sure the tool is just inside the lip on the very back of the tool.
2. Once step 1 is fully done, we need to add M3 BHCS via the front to the front and screw them in. Optionally add 5x2 magnets to the head of the bolts on the front of the cowl (Steel bolts are required for this option). Tighten the bolts until it touches the bolts/magnets on the front cowl of the tool.

NOTE: Stealthburner shown, other tool heads user different screw sizes and placement.

18

M3 BHCS; Magnets
Blackbird Medium; Dragonburner; Blackbird Small; Stealthburner

## NEXT STEPS

ASSEMBLY COMPLETED!

Congratulations, now restart at Step 1 for as many tools as you are installing on your toolchanger.

### https://github.com/DraftShift/ModularDock/tree/main/config

NEXT STEP: CONFIGURATION

This manual is designed to be a reference manual for the build process of the Modular Dock.

The configuration you’ll require for the docking sequence can be found on our github page. We recommend starting there.

19

# DRAFTSHIFT DESIGN

DISCORD; discord.gg/jJs73c6vSc

GITHUB
github.com/DraftShift

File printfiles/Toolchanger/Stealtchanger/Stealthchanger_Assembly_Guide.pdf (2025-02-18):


# STEALTHCHANGER V1 BUILD GUIDE

# Because you can never have too many tools

for any project.

# VERSION 2024-04-12

# DRAFTSHIFT DESIGN

PREFACE | GITHUB.COM/DRAFTSHIFT/STEALTHCHANGER

Before you begin on your journey, a word of caution.

In the comfort of your own home you are about to assemble a robot. This machine can maim, burn, and electrocute you if you are not careful. Please do not become the first STEALTHCHANGER fatality. There is no special Reddit flair for that.

Please, read the entire manual before you start assembly. As you begin wrenching, please check our Discord channels for any tips and questions that may halt your progress.

Most of all, good luck!

THE DRAFTSHIFT DESIGN TEAM

2

## TABLE OF CONTENTS

Introduction | 04
Hardware | 07
Shuttle | 08
Stealthburner | 11
Dragonburner | 14
Attaching to Carriage | 17
End Stop Options | 21
Next Steps | 22

3

## GITHUB.COM/DRAFTSHIFT/STEALTHCHANGER

## INTRODUCTION

PART PRINTING GUIDELINES

The Voron Team has provided the following print guidelines for you to follow in order to have the best chance at success with your parts. The StealthChanger Team recommends to follow the same standards. There are often questions about substituting materials or changing printing standards, but we recommend you follow these:

3D PRINTING PROCESS
Fused Deposition Modelling (FDM)

MATERIAL
ABS

LAYER HEIGHT
Recommended: 0.2mm

EXTRUSION WIDTH
Recommended: Forced 0.4mm

INFILL TYPE
Grid, Gyroid, Honeycomb, Triangle or Cubic

INFILL PERCENTAGE
Recommended: 40%

WALL COUNT
Recommended: 4

SOLID TOP/BOTTOM LAYERS
Recommended: 5

4

## INTRODUCTION

FILE NAMING

By this time you should have already downloaded our STL files from the StealthChanger GitHub. You might have noticed that we have used the Voron naming convention for the files. This is how to use them.

PRIMARY COLOUR

Example part_x4.stl

These files will have nothing at the start of the filename.

ACCENT COLOUR

Example [a]_part.stl

We have added “[a]” to the front of any STL file that is intended to be printed with accent colour.

QUANTITY REQUIRED

Example [a]_part_x4.stl

If any file ends with “_x#”, that is telling you the quantity of that part required to build the machine.

HOW TO GET HELP

If you need assistance with your build, we are here to help. Head on over to our Discord group and post your questions. This is our primary medium to help STEALTHCHANGER Users and we have a great community that can help you out if you get stuck.

### https://discord.gg/jJs73c6vSc

5

## INTRODUCTION

REPORTING ISSUES

Should you find an issue in the documentation or have a suggestion for an improvement please consider opening an issue on GitHub (https://github.com/DraftShift/Stealthchanger/issues). When raising an issue please include the relevant page numbers and a short description; annotated screenshots are also very welcome. We periodically update the manual based on the feedback we get.

THIS IS JUST A REFERENCE

This manual is designed to be a simple reference manual. Building a StealthChanger can be a complex endeavour and for that reason we recommend downloading the CAD files off our Github repository if there are sections you need clarification on. It can be sometimes be easier to follow along when you have the whole assembly in front of you.

### https://github.com/DraftShift/StealthChanger

6

## HARDWARE REFERENCE

BUTTON HEAD CAP SCREW (BHCS) Metric fastener with a domed shape head and hex drive. Most commonly found in locations where M5 fasteners are used. ISO 7380-1 | SOCKET HEAD CAP SCREW (SHCS) Metric fastener with a cylindrical head and hex drive. The most common fastener used on the Voron. ISO 4762
FLAT HEAD COUNTERSUNK SCREW (FHCS) Metric fastener with a cone shaped head and a flat top. ISO 10642 | HEAT SET INSERT Heat inserts with a soldering tip so that they melt the plastic when installed. As the plastic cools, it solidifies around the knurls and ridges on the insert for excellent resistance to both torque and pull-out.
BUSHING/SLEEVE BEARING Brass cindered are the most common. They should be self lubricating and metal construction. | ROUNDED DOWEL PIN Steel rounded dowel pin, These are commonly using in furniture construction. Female threaded versions are optional.

MAGNET Metric round button neodymium magnet used on the Voron. N52 is highly recommended.

7

## SHUTTLE

INSERT BUSHINGS

Inspect the bushing hex holes, make sure they are 6mm between walls of the hex. Make sure the hex is well formed. This is an important step as it could cause misalignment later on.

Apply a small amount of epoxy or glue to the inside of the hex (be sparing as you do not want any inside the the bushing).

Push the bushing into the hex and let sit until the epoxy or glue dries.

NOTE: Wipe any excess away and make sure none goes inside the bushing.

NOTE: you may be able to friction fit the bushings to test before your affix them permanently.


INSERT MAGNETS

Apply a small amount of epoxy or glue to the inside of the opening.

Push the magnet into the opening and let sit until the epoxy or glue dries.

NOTE: you may be able to fiction fit the magnets to test before your affix them permanently.

## 4 ID x 6 OD x 6mm Bushing

## 6x3mm Magnet

8

## SHUTTLE

Heat Set

OPTIONAL INSERT HEAT SET

Optionally insert the end stop heat set. Only required if you are not using sensorless.


OPTIONAL SPINE SCREWS

Optionally screws can be inserted to add rigidity to the shuttle if your not happy with it’s stiffness

## M3x40mm SHCS

9


FINISHED SHUTTLE

This is the finished shuttle with options shuttle keeper (later in this manual) and the optional Hall Effect end stop attachment (later in this manual).

## SHUTTLE

10

## STEALTHBURNER

INSERT HEAT SETS

Start by setting the heat sets.


INSERT DOWEL PINS

Inspect the pin hex holes, make sure they are 4mm between walls of the hex. Make sure the hex is well formed. This is an important step as it could cause misalignment later on.

Apply a small amount of epoxy or glue to the inside of the hex.

Push the pins into the hex and let sit until the epoxy or glue dries.

NOTE: You may be able to friction fit the pins to test before your affix them permanently.

NOTE: You should test fit the pins onto the plate and the plate with the pins on the shuttle before making them permanent.

NOTE: Make sure to wipe away any excess so your can have a full sit into the bushings.

## Heat Set

## 4 OD x 12mm Pins

11

## STEALTHBURNER


PRELOAD SCREWS

Insert the preload screws all the way, do not over tighten, we will set these later in this document (See Next Step). These just thread into the printed part without a heat set.

NOTE: These screws need to be magnetic like used in Voron Tap.

INSERT MAGNETS

Apply a small amount of epoxy or glue to the inside of the opening.

Push the magnet into the opening and let sit until the epoxy or glue dries.

NOTE: you should be able to fiction fit the magnets to test before you affix them permanently.

## 6x3mm Magnet

## M3x8mm FHCS

12

## STEALTHBURNER


PREPARE FOR STEALTHBURNER

Install the screws to click on the stealthburner bottom piece. See stealthburner guild for screw sizes.


FINISHED TOOL PLATE

This is the finished stealthburner tool plate now continue with the official stealthburner guide from the Voron team.

NOTE: you may need to use longer screws when attaching the CW2.

13

## DRAGONBURNER

INSERT HEAT SETS

Start by setting the heat sets.


INSERT DOWEL PINS

Inspect the pin hex holes, make sure they are 4mm between walls of the hex. Make sure the hex is well formed. This is an important step as it could cause misalignment later on.

Apply a small amount of epoxy or glue to the inside of the hex.

Push the pins into the hex and let sit until the epoxy or glue dries.

NOTE: You may be able to friction fit the pins to test before your affix them permanently.

NOTE: You should test fit the pins onto the plate and the plate with the pins on the shuttle before making them permanent.

NOTE: Make sure to wipe away any excess so your can have a full sit into the bushings.

## HeatSet

## 4 OD x 12mm Pins

14

## DRAGONBURNER


PRELOAD SCREWS

Insert the preload screws all the way, do not over tighten, we will set these later in this document (See Next Step). These just thread into the printed part without a heat set.

NOTE: These screws need to be magnetic like use in Voron Tap.

INSERT MAGNETS

Apply a small amount of epoxy or glue to the inside of the opening.

Push the magnet into the opening and let sit until the epoxy or glue dries.

NOTE: you should be able to fiction fit the magnets to test before you affix them permanently.

## 6x3mm Magnet

## M3x8mm FHCS

15

## DRAGONBURNER

FINISHED TOOL PLATE; guide from chirpy2605’s github.; M3x12mm BHCS

Install the spacer on to the cowl first, then using the front cowl bolt add the backplate.

This is the finished dragonburner tool plate now continue with the official dragonburner

NOTE: you may need to use longer screws when attaching the cowl.

16

## ATTACHING TO CARRIAGE

SHUTTLE KEEPER

This is the easiest option, you loop the belts through the keeper, and then install it between the carriage and the shuttle using BHCS screws. You need longer screws to be able to go through both. Make sure you tighten the shuttle well.

Now adjust your belts as per standard Voron adjustments using the idlers.

OPTIONS

There are 2 options when it comes to attaching the belts and installing the shuttle to the X carriage.

1. You can use the shuttle keeper, this is the easiest way to install it the belts and allows for you to remove the shuttle without having to remove the belts. The down side is that you lose about 5mm of Y travel.
2. You can use the belt Helper tool to push the belts behind the shuttle and tighten the carriage screws which will pinch the belts between the carriage and the shuttle.

We will go though both options in this section but you only need to choose one.


FRONT

BACK

INSTALL ORIENTATION

17

## ATTACHING TO CARRIAGE

BELT HELPER

Heat Set

INSERT HEAT SETS

Start by setting the heat sets.

## Heat Set

18

## ATTACHING TO CARRIAGE

INSERT SCREWS

Add the belt clamps, make sure to match the icons with the right sides.

Install the belt clamp screws loosely.

Install the clamping screws loosely.


## M3x20mm SHCS


## M3x10mm SHCS

19

## ATTACHING TO CARRIAGE


INSERT THE BELTS

Insert the belts, Making sure that there are 15 belt ridges on the inside of the helper. Makes sure you tighten the belt clamps well so the belt doesn’t slip.

NOTE: there is no need to pull hard the belts, just make sure there is no slack, if you pull too hard at this point you will over tighten the belts a could damage other components.

Next start to tighten the top and bottom screws, make sure your try to do this evenly until you measure 6mm between left and right side at the top and bottom evenly.

INSTALL THE SHUTTLE

NOTE: you must wait until after the shuttle is installed before adding any end stops if you are using one.

M3x8mm BHCS w/o Keeper; M3x12mm BHCS w/Keeper

The belt ends should be nearly touching, at this point install the shuttle and tighten it to the carriage using BHCS screws as per Voron Manual. Make sure things are nice and tight before you start to replace the helper.

Once you are ready, slowly undo the top and bottom screws evenly. Once there is enough slack you may remove the clamps on the belts and remove the helper.

Now adjust your belts as per standard Voron adjustments using the idlers.

20

## END STOP OPTIONS

OPTIONS

There are a few options when it comes to end stops. Hall Effect is a Voron stands as well as end stop switches. The team doesn’t provide the switch side, but we do have attachment points for and suppose to most common activation arms.

NOTE: more options may be available and are welcome.

HALL EFFECT
INSERT MAGNETS

M3x8mm BHCS

Apply a small amount of epoxy or glue to the inside of the opening.

Push the magnet into the opening and let sit until the epoxy or glue dries.

NOTE: you should be able to fiction fit the magnets to test before you affix them permanently.


INSTALL THE END STOP ACTIVATION ARM

Simply screw it into the back side of the shuttle.

NOTE: Hall Effect and X Switch pictured.

## 6x3mm Magnet

21

## NEXT STEPS

ASSEMBLY COMPLETED!

The last step is to set preload. This should be done on each tool separately as it’s meant to help counter inconsistencies/variances in the parts.

Preload is created with the 2 countersunk screws in the tool plate. These 2 screws need to be magnetic and will make contact with the magnets in the shuttle. This adds 2 more wider points of contact at the base while also pre loading the sleeves/bearings. To adjust them screw them all the way in, then slowly unscrew them 1/4 turn at a time (keeping each side even) until the tool no longer engages its self right away. Once you reach a point where this happens, screw them back in 1/4 turn. Each tool needs to be adjusted separately as printing irregularities can happen and this will allow you to compensate for it. You may want to test and readjust these from time to time.

### https://github.com/DraftShift/Stealthchanger/wiki/Installation

22

NEXT STEP: SETUP & CALIBRATION

This manual is designed to be a reference manual for the build process of a StealthChanger.

The software setup and other initial setup steps with your new toolchanger can also be found on our github page. We recommend starting there.

Enjoy your toolchanger.

23

GITHUB

github.com/DraftShift

DISCORD

discord.gg/jJs73c6vSc

# DRAFTSHIFT DESIGN

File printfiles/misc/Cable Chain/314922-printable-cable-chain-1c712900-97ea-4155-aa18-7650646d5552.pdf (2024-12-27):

3D MODEL ONLY

## Summary

Printable cable chain v2.0 can used for voron

3D Printers (https://printables.com/model?categoryId=1) | > | Voron Upgrades (https://printables.com/model?categoryId=137)
Tags: | cable | chain | ender | cablechain | voron

I would like to present you version 2.0 of the design.

I received some feedback from several users after they printed my

previous design version, thank you for that!

this has given me new insights for expansion and improvements of the
design.

All parts have been tested by me for printability, some tolerances have

also been adjusted between the parts for a better fit.

Tom van der Geest (https://printables.com/@TomvanderGeest)

## Printable Cable

# Chain

### VIEW IN BROWSER (https://printables.com/model/314922-printable-cable-chain)

updated 4. 9. 2023 | published 20. 4. 2023


What has changed in the design:

Additional end pieces with two mounting holes have now been added to

## the design

and the design of end (a) is adapted to the same shape as end (b).

Sharp corners are rounded for better print quality.


The coupling part is chamfered for easier attachment


Dimensions 40 degree chain:

Dimensions 30 degree chain:

The dimensions of a chain are: Wide 17mm High 14.3mm


# Model files

A design for printing the generic

cable chain yourself.

Can only turn in one direction.

### Material: PLA, ABS or ASA. (ASA

recommended).

layer height recommended:

0.2mm.

Extrusion width recommended:

0.4mm.
Fill Type: Grid, Gyroid,

Honeycomb, Triangle or Cubic.

Infill percentage recommended:

40%.

Wall count recommended: 4.

Solid top/bottom layers recommended: 5.

Printable without support!

Now also available → Bed and Frame Cable Chain Mount (https://www.printables.com/model/426205-bed-and-frame-cable-chain-mount)

Please follow more designs soon !!!

### - 04-2023 update v2.0

chain⁻link-30-degree⁻angle.stl

chain⁻link-40-degree⁻angle.stl

fixed-end-2-holes⁻b.stl

## License

This work is licensed under a

Creative Commons (4.0 International License) (http://creativecommons.org/licenses/by-nc-sa/4.0/)

fixed-end-2-holes⁻a.stl

chain⁻link-55-degree⁻angle.stl

unfixed-end-2-holes⁻b.stl

unfixed-end-2-holes⁻a.stl

fixed-end-3-holes⁻b.stl

fixed-end-3-holes⁻a.stl

unfixed-end-3-holes⁻b.stl

unfixed-end-3-holes⁻a.stl

Attribution—Noncommercial—Share Alike (http://creativecommons.org/licenses/by-nc-sa/4.0/)

### ✖ | Sharing without ATTRIBUTION

✔ | Remix Culture allowed
✖ | Commercial Use
✖ | Free Cultural Works
✖ | Meets Open Definition

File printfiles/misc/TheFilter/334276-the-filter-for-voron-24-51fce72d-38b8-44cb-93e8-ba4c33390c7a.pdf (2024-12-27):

3D MODEL ONLY

## Summary

Designed by my friend Nate (nateb16). Updated configuration file to improve Filter function, longevity and performance.

3D Printers (https://printables.com/model?categoryId=1) > Voron Parts & Upgrades (https://printables.com/model?categoryId=137)

Tags: | filter | heatedchamber | voron | voron24 | bedfan

My friend nateb16 designed this. The Git is VoronUsers/printer_mods/ nateb16/THE_FILTER at master · nateb16/VoronUsers (github.com) (https://github.com/nateb16/VoronUsers/tree/master/printer_mods/nateb16/THE_FILTER)

NOTE: Latest revision/files will always be posted to GitHub first, and updated here as time permits.

*** Disclaimer: As with all printer mods, we are not responsible. Use at your own risk. That said, I have been using The Filter for a year and a half, POGOs for over a year, with no issues, improved chamber heating and reduced fumes. ***

UPDATE 7/1/2023: Updated Macro. Steps for use:

Save in configuration folder using the name you like. Mine is TheFilter.cfg.
Add [include TheFilter.cfg] to your printer.cfg file.
Open file and edit the pin used on your MCU.

AKinferno (https://printables.com/@AKinferno)

## THE FILTER, for Voron 2.4

VIEW IN BROWSER (https://printables.com/model/334276-the-filter-for-voron-24)

updated 24. 6. 2024 | published 24. 6. 2024

1.

2.
3.

Contact me if it doesn't work properly, or if you have suggestions. But I think I have it down.

Description of how it works in the 'AKINFERNO ADDS' section at the bottom.

UPDATE 4/25/2023 (Instructions for fan wiring/pogo and my macro)

My verison of these instructions are at the bottom, under 'AKINFERNO ADDS' section.

UPDATE: 4/13/2023 (Experimental parts added by me)

I added a couple variants. I thickened the lines on the lid so they are .8mm instead of .4mm. Intended to ensure lighter colors stood out when doing color swaps. And the spacer clips always broke on me. So, I redesigned them using the Voron Deck supports. Insert them sideways and rotate down. They won't slide or break. I will likely make a fork on the Git and post all my mods to the Experimental folder so Nate's work stays intact.

UPDATE: 2/5/2023 (Fysetc Kit Model only)

With feedback from the Voron community. A number of things have been addressed. 1) The exhaust has been changed and optimized to prevent the loss of pellet issue, and improve filtering performance. The trade off is heat up times and overall chamber heating performance is slightly affected. Will update graphs after testing and leave V1 in archive. 2) The mounts for pogo connector's have been changed to fit the aliexpress listings. 3) Screw holes have been added to secure the fans and the lid, if desired. 4) The install instructions have also been updated for clarity.

UPDATE: 1/11/2023

Thanks to devsfan1830#3401 on Discord for finding and fixing an issue with the Standard 2 fan model, and making a similar single fan model for the sides, which has been added below.

UPDATE: 12/26/2022

With feedback from members of the community, a number of things have been addressed. First, the exhaust has been changed and optimized to improve the loss of pellet issue as well as improve filtering performance. The trade off for these modification is heat up time and overall heating performance is slightly affected. The mounts for connector's have also been changed to fit the aliexpress listings. I have added holes to secure the fans if desired. The lid still lacks screws for aesthetic reasons. Wiring channels for the two fan version have also been drastically altered due to confusion and overall jankyness.

4.

Nateb16 also updated the install instruction for clarity.

ABOUT

THE FILTER is a custom mod of Nate's own design. He was initially inspired to embark on this project after his Nevermore melted. It is a hybrid of Andrew Ellis's bed fan's chamber heating, and the Nevermore's charcoal filtering, in a completely custom housing. He created two designs; a two 5015 fan version and a 3 fan version for Fysetc beds (since they have non standard bed mount spacing). Both feature a high capacity for pellet charcoal in a two piece model with a bracket using a minimal amount of fasteners. It is mounted from the front to DRASTICALLY improve heating of your printer chamber by blowing air over the bottom of the bed. He also wanted it to be easily removable, so it features an optional magnetic quick disconnect using POGO connectors, which he believes is a first for a mod of this kind. This connector makes removal (during PLA prints) and maintenance quick and easy. It has been tested extensively with over 40 hours of runtime and 50 connects and disconnects. Its high airflow and compact design make it melt and warp resistant. Using 3d printed spacers it is also thermally isolated from the printer frame.

Testing

Rough estimates found during testing (results vary on how well your printer is insulated and how large it is as well)

Time the printer took to reach 40c

Stock VORON 2.4 350mm - 55 minutes
Nevermore VORON 2.4 350mm - 40 minutes
THE FILTER VORON 2.4 350mm - 12 minutes

Quick statistics graph (courtesy of Discord user akinferno#3062)

Testing heat up time to 40°C

•
•
•


Parts Required

(2-3) 5015 fans 24v
(ferrule kit)
(1) 2 pin microfit molxex if not using the POGO connector
(1) MISC heatshrink and solder (best) or Solder heatshrink tubing (better) or buttsplices (ok)

pogo connector and cord from ali-express

(1) *** Working on sourcing proper part. Listing has changed and may not be suitable for installation. Currently investigating alternatives *** (6/24/2024)

Installation

Install instructions found with applicable models

If Using magnetic connector's:

Print Soldering Jig (connector is magnetic and is very hard to solder with out being secured)

center pin is positive
side pins are GND

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
place connector into jig and tape down to more easily attach wires

If applicable Cut USB connector off exposing red and black wire otherwise proceed to step 3
Crimp on ferrules and press the end of the power cable into 3d printed mounting bracket (use super glue if the connector feels to loose)
Connect to MCU and adjust your config (I encourage the filter to be set up using andrew ellis bed fan macro)

IMPORTANT

CONNECT WIRES TO SPARE HOTEND PORTS TO PROTECT THE MCU in case of accidental disconnects for the filter. ** explained in AKinfernos Adds

DO NOT REMOVE THE PRINTED LID WHILE THE BUILDPLATE IS WARM (DOING SO INTRODUCES BOWING TO THE PART RESULTING IN A BAD SEAL AND TERRIBLE PERFORMANCE)

Sample config and setup instructions (pulled from andrew ellis github)

https://github.com/VoronDesign/VoronUsers/blob/master/printer_mods/Ellis/Bed_Fans/Klipper_Macros/bedfans.cfg (https://github.com/VoronDesign/VoronUsers/blob/master/printer_mods/Ellis/Bed_Fans/Klipper_Macros/bedfans.cfg)

A pre configured macro with modified variables is provided be sure to Add [include bedfans.cfg] to your printer.cfg and adjust the pin or follow direction below.

1) Place the .cfg file in the same directory as your printer.cfg file.
2) Add [include bedfans.cfg] to your printer.cfg.
3) Change pin for your fans in the second section.

This is intentionally left blank so that it will error if you don't fill it in.

4) Configure the options in the first section:

variable_threshold sets the bed temp threshold at which your bed fans will be used.
Default is 100C (so it does not enable for PLA)
variable_slow sets the fan speed for when the bed is heating. variable_fast sets the fan speed for when the bed is at
temperature.

NOTE: Included text version of my config, which is slightly modified to run fans at low when printing PLA/PETG, to prevent bed heat from warping lid.

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
Prototype Install Picture's (Current CAD and models have minor cosmetic changes compared to these picture)

Credits

Designer: nate#5815

Beta Tester/Sounding Board: akinferno#3062

Andrew ellis (Ellis #4980) for inspiration and for a macro that I couldn't make myself https://github.com/VoronDesign/VoronUsers/tree/master/printer_mods/Ellis/Bed_Fans (https://github.com/VoronDesign/VoronUsers/tree/master/printer_mods/Ellis/Bed_Fans)

The Nevermore (click the link to learn about VOC's) https://github.com/nevermore3d/Nevermore_Micro (https://github.com/nevermore3d/Nevermore_Micro)

CAD files located on Github linked at top.

SINGLE FAN VERSION INSTRUCTIONS

Modification created by devsfan1830#3401 on the Voron Discord based on the CAD files for the standard spacing version.

Note, some details may not match whatever the current models are for the other variants. If you find an issue or an inconsistency, contact devsfan1830#3401 via discord PM. No need to bug nate :) .

Print the same as the originals. Note, you MUST print the left and right versions of each file. Mirroring any STL will result in misalignments. Orientation should be self-explanantory but it's oriented as if you were looking at your printer from the front.

The holes for the magnetic connector are based upon the aliexpress item linked above. There may be some variances in prints. If something doesn't fit right, please add a comment or PM devsfan1830#3401 on Discord or use the CAD files on the Github to make adjustments.

IMPORTANT

IT IS STILL IMPORTANT TO NOT CONNECT THESE FANS TO THE FAN HEADERS USE A HOTEND PORT FOR DURABILTY AND TO PREVENT ACCIDENTAL DAMAGE TO THE MCU

REQUIRED PARTS

FAN SPLITTER BOARD FROM KB3D (NOT AFFLIATED JUST LIKE THESE GUYS)

https://kb-3d.com/store/electronics/631-fan-splitter-expansion-pcb-1658867098563.html (https://kb-3d.com/store/electronics/631-fan-splitter-expansion-pcb-1658867098563.html)

•

AKINFERNOs ADDS

Nate is a friend, and didn't have or want a Printables account, which is why I posted TheFilter here. He updated the Git, I update this. TheFilter is his creation, so I try to copy his Git word for word, but have added this section to clearly identify what information comes from me. Eveything above is from his Git.

Why use the spare hotend terminal instead of a fan terminal?

During testing, we realized that if your pogos aren't lined up exactly, and you connect or disconnect the fan while energized, there is a change for a brief short, right before the magnets connect. This was enough to short out the fan terminals on your MCU, never to work again. The hotend has much more robust power protection circuitry. It won't short out the board. At worst, it would pop the fuse, which we never saw happen during testing. So use the fan terminal at your own risk. For that matter, do all this at your own risk. But know we have not heard of anyone having any issues with the pogos on the hotend terminals.

My Pogo wiring Instructions

So, below is a poorly drawn wiring diagram. The purple is the grooves in the base. All fans have both positive and negative wires, which you can split once they enter the rear wire management area. I only drew the positive wire paths. You can see my two butt splices in the photo. Positive on the right, negative on the left.

Left fan - Green

Center fan - Yellow

Right fan - Blue

Pogo connector - Orange


Nate's instructions are above, I am gonna express them in my own words. My instructions refer to the photo above, with the color change versions of the lids. Worth noting, that is the same body in both pics. A different lid can completely change the look of your Filter!

Step 1 - Print the pogo soldering jig and push the pogo into it. The wire has to be long enough to reach the back wire management area and at least a couple inches to either side. I left about 6". I didn't want to mess with the pogo again, and since I would have to cut off the butt splice, I wanted to have plenty of copper available. There is plenty of room back there to tuck some extra wire.
Step 2 - Don't forget your heats shrink! Solder the wires to the terminals. I soldered positive to the center post and negative to one of the side terminals.
Step 3 - Pull the cable out of the jig and feed iy through the front of TheFilter body. If you have drooping filament from poor bridging, you may have to clear that out. If you break a support or two... I won't tell. It will still work fine. Don't ask how I know.
Step 4 - Once it reaches the cable management area, split the positive and negative to the side they belong, and attach them to your fan terminals. Nate recommends soldering. I prefer the lazy butt splices. I have enough excess from step 1 not to worry about it :p
Step 5 - Install the mounting bracket. My pogo had a thick grommet around it, so it didn't fit flush with the bracket. It did however taper down, so I pushed it in anyway. Once secured, I mounted it in place and it works great. The pogo sits about an inch in front of the mounting bracket, but is perfectly aligned, so not ordering another one. If you got the 90degree plug, the 1.1 bracket in the ‘Stock Filter’ folder appears to support that cable.
Step 6 - Install a config file. Mine is located in my akinferno/VoronConfig: Files for my new Voron (github.com) (https://github.com/akinferno/VoronConfig) TheFilter.cfg is my file for this mod. Some people are happy with the Nevermore macro, others use Ellis' BedFan macro. I think mine works perfect now. It is a slightly modified version of Ellis'. You have to add that as an [include TheFilter.cfg] in your printer.cfg. Adjust the pins and thresholds in the top section of your printer. BE AWARE: I am not afraid to play around with these files. I usually only update the Git when I get it working properly, so it should be safe, but use my files at your own risk. I don't know enough to make big changes without testing, but do know enough about Jinja to break things. I also lack sufficient fear to keep me from tweaking things :p

How my macro works right now: When bed temp is set to 60C or higher, the fan kicks on to 30%. Once the target temperature is reached... if target is 100C or greater, it jumps up to 100%. Those thresholds can be changed right at the top of the file. With Ellis', if you set it to 60, it kicks on to 100% when that temp is reached too. My macro just keeps the fan at 30% for temps between the low and high thresholds. I didn't want the extra chamber heat when printing PLA. Just enough airflow so the lid won't warp.

UPDATE: In Ellis' macros, when the Target is 0C, the fans turn off. With my macro, there is now an offthreshold. The fans drop to the slow speed until the bed temperature falls below that temperature. This will ensure the fans keep running to 1) filter the air while the chamber is warm, 2) ensure airflow through TheFilter while the bed is hot enough to warp the lid. This status is checked every 5min. So, they may stay on slightly below the threshold. That is easily adjusted too.

I set it to 45 by default. Just be sure the temperature is above the ambient temperature of your bed or it will stay on forever.

-------------------------------------------OLD UPDATES---------------------

The Filter Stock Body V1.2 UPDATE: 12/21/2022

Edited lids to shave a bit from edge. This should ensure a good fit, even with a slightly squished first layer.
Added screw holes for fans. These aren't required, but have been requested. Ensure you remove the tops of the 5015 fans or the lid will not fit properly. Non-screw version is in Archive folder.

•

•

## Model files

Single Fan (Side Fan) Model; 6 files; the-filter_fysetc_body_2_0.stl; the-filter_fysetc_lid_2_0.stl; the-filter_fysetc_bracket_2_0.stl; the-filter_spacer-25mm.stl; the-filter_pogo_soldering-jig.stl; the_filter_single_left-side-body.stl; the_filter_single_left-side-lid.stl

Fysetc Edition (Wider bed supports than Voron manual) | 5 files

Standard Voron Spacing | 3 files
- V1.4 - Thanks to Reddit user devsfan1830 for finding and fixing gap in previous stl.
- V1.1 - Made lid easier to print. Shaved small amount from edges. Updated 12/21/2022
- V1.1 - modified to fit listed connector.
- CAD Files | 3 files
- 3 Jan 2023

the_filter_single_left-side-mag-mount.stl

the_filter_single_right-side-body.stl

the_filter_single_right-side-lid.stl

the_filter_single_right-side-mag-mount.stl

the-filter_stock_body_1_4.stl

the-filter_stock_lid_1_1.stl

the-filter_stock_bracket_1_1.stl

the_filter_standard_spacing-v61.step

- 29 Jan 2023
- 23 Jan 2023
- Experimental | 2 files
- This is AKinferno's mod, uses the clip from the Voron deck supports.
- This is AKinferno's mod with a .8mm high fractal pattern (instead of .4mm)
- Archive_Obsolete | 11 files
- V1.0 Original
- V1.3-Improved cable routing and reduced mesh size, and magnet holder. Updated 12/27/2022
- V1.0 - Original
- V1.0 - Original lid

the_filter_fysetc_edition-v10.step

single-fan-fixed-mount.step

updated_25mm-spacer.stl

the-filter_fysetc_lid_2_0_x1.stl

the-filter_stock_mounting-bracket_v1.stl

the-filter_stock_body_1_3.stl

the-filter_fysetc_body_v10.stl

the-filter_fysetc_lid_v10.stl

## Other files

- V1.0
- V1.0
- Version 1.1 update: 12/10/2022
- V1.2 - Added fan screw holes, ridge so charcoal won't roll out. 12/21/2022
- V1.1 Added screw holes for fans. Updated 12/21/2022
- V1.1 - Easier to print. Shaved small amount from edges. Updated 12/21/2022
- Klipper config I came up with, based on Ellis' BedFan config. Rename it TheFilter.cfg the-filter_stock_body_v10.stl

the-filter_stock_lid_v10.stl

the-filter_stock_body_1_1.stl

the-filter_stock_body_1_2.stl

the-filter_fysetc_mounting-bracket.stl

the-filter_fysetc_body_1_1.stl

the-filter_fysetc_lid_1_1.stl

thefiltercfg.txt

## License

This work is licensed under a
Creative Commons (4.0 International License)

Attribution-NonCommercial (http://creativecommons.org/licenses/by-nc/4.0/)

✖ | Sharing without ATTRIBUTION
✔ | Remix Culture allowed
✖ | Commercial Use
✖ | Free Cultural Works
✖ | Meets Open Definition

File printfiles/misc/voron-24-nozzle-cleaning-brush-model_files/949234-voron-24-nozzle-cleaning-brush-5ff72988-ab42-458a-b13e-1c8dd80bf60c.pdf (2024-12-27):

3D MODEL ONLY

## Summary

As the title states, another nozzle cleaning brush for Voron 2.4.

3D Printers (https://printables.com/model?categoryId=1) > Voron Parts & Upgrades (https://printables.com/model?categoryId=137)

Tags: | brush | brass | voron | brushholder | nozzlecleaner
voron24 | brassbrush | fystec

Another nozzle cleaning brush for Voron 2.4. I couldn't find anything that fit well enough and was sturdy enough. I think my printer is tuned pretty well so if you have assembly issues please reference Ellis's tuning guide and see if that corrects them. Standard Voron print settings.

It's made to fit these brushes. I also have PEEK bed screws with the 10mm spacers but should clear almost anything that also allows Nevermore to be under the bed.

https://www.aliexpress.us/item/3256805472322461.html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 (https://www.aliexpress.us/item/3256805472322461.html)

https://www.fabreeko.com/products/peek-heated-bed-feet-for-voron-2-4-trident-by-fystec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 (https://www.fabreeko.com/products/peek-heated-bed-feet-for-voron-2-4-trident-by-fystec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)

James C. Foley (https://printables.com/@JamesCFoley_401007)

## Voron 2.4 Nozzle Cleaning Brush

VIEW IN BROWSER (https://printables.com/model/949234-voron-24-nozzle-cleaning-brush)

updated 20. 7. 2024 | published 20. 7. 2024

## Model files

I used M3x6 screws and hammerhead nuts to secure it. M3x8 screws may work but I didn't test them.

## License

This work is licensed under a
Creative Commons (4.0 International License)

Attribution-NonCommercial (http://creativecommons.org/licenses/by-nc/4.0/)

✖ | Sharing without ATTRIBUTION
✔ | Remix Culture allowed
✖ | Commercial Use
✖ | Free Cultural Works
✖ | Meets Open Definition

voron-24-nozzle-cleaning-brush-v4.step

nozzle-cleaning-brush-main-body.stl

nozzle-cleaning-brush-slide-door.stl

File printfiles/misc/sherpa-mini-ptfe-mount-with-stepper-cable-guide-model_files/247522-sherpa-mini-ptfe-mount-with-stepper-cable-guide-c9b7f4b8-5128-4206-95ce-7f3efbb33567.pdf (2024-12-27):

3D MODEL ONLY

## Summary

Mount for Sherpa Mini extruder direct drive with guide for stepper motor cables.

3D Printers (https://www.printables.com/model?categoryId=1) > 3D Printers - Upgrades (https://www.printables.com/model?categoryId=2)

Tags: mini | ptfe | strainrelief | sherpa

Uses existing left side extruder to stepper casing for mounting, as right side screw will collide with the idler arm. I tried the original model and the right side will just break if you try to screw it tight. You will need to glue the cable guide. Print without supports, flat side facing down.

also included the version for right side mounting too, if you're keen on using it.

uses generic PC4-01 through pneumatic connectors. Thread is M10x6mm.

remixed from https://www.thingiverse.com/thing:5155474.

john doe (https://www.printables.com/social/319398/about)

## Sherpa Mini PTFE mount with stepper cable guide

VIEW IN BROWSER (https://www.printables.com/model/247522-sherpa-mini-ptfe-mount-with-stepper-cable-guide)

updated 25. 7. 2022 | published 25. 7. 2022

## Model files

- left side mounting only
- both sides mounting

Find source .stl files on Thingiverse.com (https://www.thingiverse.com/thing:5155474)

## License

This work is licensed under a GNU

General Public License v2.0 (http://www.gnu.org/licenses/old-licenses/gpl-2.0.html)

✖ | Sharing without ATTRIBUTION
✔ | Remix Culture allowed
✔ | Commercial Use
✔ | Meets Open Definition
ℹ | Share under the same license new-sherpa-ptfe-mount-v2.stl

sherpa-cable-v1.stl

sherpa-ptfe-mount-v1.stl

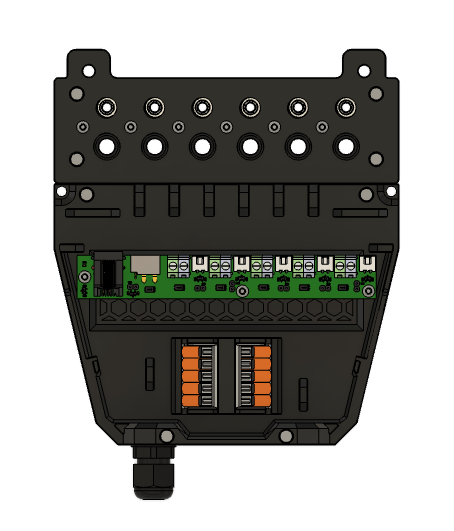
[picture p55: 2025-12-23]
printfiles/Toolchanger/DraftShiftCableManagement/STLs/FannyPack/media/FannyPack_CEB.png

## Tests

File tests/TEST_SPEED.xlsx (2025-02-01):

500 => 5000 | Start Pos | End Pos | Diff | 750 => 5000 | Start Pos | End Pos | Diff
stepper_x: | 57598 | 57599 | -1 | stepper_x: | 57594 | 57596 | -2
stepper_y: | -41922 | -41923 | 1 | stepper_y: | -41918 | -41922 | 4
stepper_z: | 43126 | 43119 | 7 | stepper_z: | 43122 | 43109 | 13
stepper_z1: | 43154 | 43147 | 7 | stepper_z1: | 43150 | 43137 | 13
stepper_z2: | 45174 | 45167 | 7 | stepper_z2: | 45170 | 45157 | 13
stepper_z3: | 43138 | 43131 | 7 | stepper_z3: | 43134 | 43121 | 13
500 => 6000 |  |  |  | 750 => 6000
stepper_x: | 57598 | 57599 | -1 | stepper_x: | 57594 | 57597 | -3
stepper_y: | -41922 | -41925 | 3 | stepper_y: | -41918 | -41923 | 5
stepper_z: | 43131 | 43121 | 10 | stepper_z: | 43119 | 43106 | 13
stepper_z1: | 43159 | 43149 | 10 | stepper_z1: | 43147 | 43134 | 13
stepper_z2: | 45179 | 45169 | 10 | stepper_z2: | 45167 | 45154 | 13
stepper_z3: | 43143 | 43133 | 10 | stepper_z3: | 43131 | 43118 | 13
500 => 7000 |  |  |  | 750 => 7000
stepper_x: | 57595 | 57597 | -2 | stepper_x: | 57594 | 57596 | -2
stepper_y: | -41919 | -41923 | 4 | stepper_y: | -41920 | -41920 | 0
stepper_z: | 43129 | 43117 | 12 | stepper_z: | 43112 | 43107 | 5
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

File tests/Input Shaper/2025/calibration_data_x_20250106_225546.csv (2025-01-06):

freq | psd_x | psd_y | psd_z | psd_xyz | zv(119.8) | mzv(75.2) | ei(41.4) | 2hump_ei(39.6) | 3hump_ei(100.0)
0.0 | 0.000e+00 | 0.000e+00 | 0.000e+00 | 0.000e+00 | 1.000 | 1.000 | 1.000 | 1.000 | 1.000
1.5 | 2.764e-12 | 6.096e-15 | 1.137e-14 | 2.781e-12 | 0.998 | 0.995 | 0.986 | 0.978 | 0.990
3.1 | 3.320e-01 | 1.573e-03 | 2.230e-03 | 3.358e-01 | 0.996 | 0.989 | 0.966 | 0.943 | 0.977
4.6 | 1.899e+01 | 2.200e-01 | 3.175e-01 | 1.952e+01 | 0.993 | 0.982 | 0.940 | 0.898 | 0.961
6.2 | 7.292e+01 | 1.184e+00 | 1.669e+00 | 7.577e+01 | 0.990 | 0.973 | 0.907 | 0.844 | 0.942
7.7 | 1.264e+02 | 2.314e+00 | 3.141e+00 | 1.318e+02 | 0.986 | 0.963 | 0.869 | 0.781 | 0.921
9.2 | 2.019e+02 | 3.024e+00 | 4.355e+00 | 2.093e+02 | 0.982 | 0.952 | 0.826 | 0.713 | 0.897
10.8 | 2.190e+02 | 3.177e+00 | 4.521e+00 | 2.267e+02 | 0.978 | 0.940 | 0.779 | 0.640 | 0.871
12.3 | 2.442e+02 | 2.813e+00 | 3.811e+00 | 2.508e+02 | 0.973 | 0.926 | 0.728 | 0.564 | 0.844
13.9 | 2.551e+02 | 2.710e+00 | 3.272e+00 | 2.611e+02 | 0.968 | 0.912 | 0.675 | 0.488 | 0.814
15.4 | 2.836e+02 | 2.382e+00 | 3.262e+00 | 2.892e+02 | 0.963 | 0.896 | 0.619 | 0.412 | 0.783
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

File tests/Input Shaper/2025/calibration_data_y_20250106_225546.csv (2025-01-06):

freq | psd_x | psd_y | psd_z | psd_xyz | zv(41.2) | mzv(41.2) | ei(49.2) | 2hump_ei(61.4) | 3hump_ei(74.0)
0.0 | 0.000e+00 | 0.000e+00 | 0.000e+00 | 0.000e+00 | 1.000 | 1.000 | 1.000 | 1.000 | 1.000
1.5 | 2.323e-15 | 2.124e-14 | 2.722e-12 | 2.745e-12 | 0.993 | 0.990 | 0.989 | 0.987 | 0.985
3.1 | 6.844e-04 | 2.376e-03 | 3.330e-01 | 3.361e-01 | 0.983 | 0.976 | 0.973 | 0.969 | 0.966
4.6 | 9.625e-02 | 2.218e-01 | 1.901e+01 | 1.932e+01 | 0.970 | 0.958 | 0.953 | 0.946 | 0.941
6.2 | 5.613e-01 | 9.452e-01 | 7.326e+01 | 7.477e+01 | 0.953 | 0.936 | 0.928 | 0.918 | 0.912
7.7 | 1.157e+00 | 1.850e+00 | 1.328e+02 | 1.358e+02 | 0.934 | 0.910 | 0.900 | 0.887 | 0.878
9.2 | 1.473e+00 | 2.807e+00 | 2.325e+02 | 2.367e+02 | 0.911 | 0.881 | 0.867 | 0.852 | 0.841
10.8 | 1.463e+00 | 3.641e+00 | 2.989e+02 | 3.040e+02 | 0.886 | 0.848 | 0.831 | 0.813 | 0.800
12.3 | 1.360e+00 | 3.970e+00 | 3.251e+02 | 3.304e+02 | 0.858 | 0.812 | 0.792 | 0.771 | 0.756
13.9 | 1.288e+00 | 2.659e+00 | 2.913e+02 | 2.952e+02 | 0.827 | 0.773 | 0.751 | 0.727 | 0.710
15.4 | 1.272e+00 | 1.842e+00 | 3.230e+02 | 3.262e+02 | 0.794 | 0.732 | 0.707 | 0.681 | 0.663
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

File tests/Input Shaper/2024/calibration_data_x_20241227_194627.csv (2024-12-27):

freq | psd_x | psd_y | psd_z | psd_xyz | zv(148.6) | mzv(110.4) | ei(140.0) | 2hump_ei(123.4) | 3hump_ei(112.8)
0.0 | 0.000e+00 | 0.000e+00 | 0.000e+00 | 0.000e+00 | 1.000 | 1.000 | 1.000 | 1.000 | 1.000
1.5 | 2.619e-12 | 4.098e-15 | 6.738e-15 | 2.630e-12 | 0.998 | 0.997 | 0.997 | 0.994 | 0.991
3.1 | 3.267e-01 | 8.142e-04 | 1.328e-03 | 3.289e-01 | 0.997 | 0.993 | 0.993 | 0.987 | 0.980
4.6 | 1.775e+01 | 1.094e-01 | 2.019e-01 | 1.806e+01 | 0.995 | 0.989 | 0.988 | 0.979 | 0.966
6.2 | 6.934e+01 | 6.059e-01 | 1.184e+00 | 7.113e+01 | 0.992 | 0.984 | 0.983 | 0.969 | 0.951
7.7 | 1.224e+02 | 1.189e+00 | 2.266e+00 | 1.259e+02 | 0.990 | 0.978 | 0.977 | 0.958 | 0.933
9.2 | 1.962e+02 | 1.550e+00 | 2.870e+00 | 2.006e+02 | 0.987 | 0.972 | 0.971 | 0.946 | 0.914
10.8 | 2.279e+02 | 1.602e+00 | 2.784e+00 | 2.322e+02 | 0.984 | 0.966 | 0.964 | 0.933 | 0.892
12.3 | 2.562e+02 | 1.276e+00 | 2.559e+00 | 2.601e+02 | 0.981 | 0.958 | 0.957 | 0.919 | 0.869
13.8 | 2.642e+02 | 1.245e+00 | 2.710e+00 | 2.682e+02 | 0.977 | 0.951 | 0.949 | 0.904 | 0.844
15.4 | 2.946e+02 | 1.101e+00 | 2.548e+00 | 2.982e+02 | 0.973 | 0.942 | 0.941 | 0.888 | 0.818
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

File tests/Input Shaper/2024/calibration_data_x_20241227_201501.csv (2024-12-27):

freq | psd_x | psd_y | psd_z | psd_xyz | zv(146.0) | mzv(107.4) | ei(136.4) | 2hump_ei(39.6) | 3hump_ei(109.6)
0.0 | 0.000e+00 | 0.000e+00 | 0.000e+00 | 0.000e+00 | 1.000 | 1.000 | 1.000 | 1.000 | 1.000
1.5 | 2.398e-12 | 3.836e-15 | 7.825e-15 | 2.409e-12 | 0.998 | 0.997 | 0.997 | 0.978 | 0.991
3.1 | 3.209e-01 | 1.154e-03 | 1.709e-03 | 3.238e-01 | 0.997 | 0.993 | 0.993 | 0.943 | 0.979
4.6 | 1.796e+01 | 1.643e-01 | 2.640e-01 | 1.838e+01 | 0.994 | 0.988 | 0.988 | 0.899 | 0.965
6.1 | 7.051e+01 | 8.583e-01 | 1.375e+00 | 7.274e+01 | 0.992 | 0.983 | 0.983 | 0.844 | 0.949
7.7 | 1.226e+02 | 1.862e+00 | 2.659e+00 | 1.271e+02 | 0.990 | 0.978 | 0.977 | 0.782 | 0.930
9.2 | 1.965e+02 | 2.533e+00 | 3.830e+00 | 2.029e+02 | 0.987 | 0.971 | 0.970 | 0.714 | 0.910
10.8 | 2.257e+02 | 2.319e+00 | 3.801e+00 | 2.318e+02 | 0.983 | 0.964 | 0.963 | 0.641 | 0.888
12.3 | 2.489e+02 | 1.994e+00 | 3.288e+00 | 2.542e+02 | 0.980 | 0.957 | 0.956 | 0.565 | 0.864
13.8 | 2.612e+02 | 1.665e+00 | 3.042e+00 | 2.659e+02 | 0.976 | 0.949 | 0.947 | 0.489 | 0.838
15.4 | 2.981e+02 | 1.482e+00 | 2.951e+00 | 3.025e+02 | 0.973 | 0.940 | 0.939 | 0.414 | 0.811
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

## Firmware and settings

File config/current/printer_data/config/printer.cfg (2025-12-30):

# includes
[include mainsail.cfg]
[include hardware/cartographer.cfg]
[include hardware/th0.cfg]
[include hardware/th1.cfg]
[include hardware/th2.cfg]
[include hardware/th3.cfg]
[include hardware/th4.cfg]
[include toolchanger/readonly-configs/toolchanger-include.cfg]
[include hardware/fans.cfg]
[include macros/macros.cfg]
[include timelapse.cfg]
[include gcode-preprocessor/preprocessor.cfg]
[include tool-crash.cfg]

# main configuration
[mcu]
canbus_uuid: 04841b8caaff

[printer]
kinematics: corexy
max_velocity: 750
max_accel: 10000
max_z_accel: 3500
square_corner_velocity: 5.0

# thermistors
# chamber
[thermistor NTC10K]
temperature1: 0.0
resistance1: 32116.0
temperature2: 40.0
resistance2: 5309.0
temperature3: 80.0
resistance3: 1228.0

# sensors
[temperature_sensor MCU]
sensor_type: temperature_mcu

[temperature_sensor SoC]
sensor_type: temperature_host

[temperature_sensor chamber]
sensor_type: NTC10K
sensor_pin: PB0
min_temp: 0
max_temp: 100

# stepper
# x-stepper (B-Motor)
[stepper_x]
step_pin: PE6
dir_pin: PE5
enable_pin: !PC14
microsteps: 32
rotation_distance: 40
full_steps_per_rotation:200
endstop_pin: tmc2209_stepper_x:virtual_endstop
position_min: 0
position_endstop: 350
position_max: 350
homing_speed: 50
homing_retract_dist: 0
homing_positive_dir: true

[tmc2209 stepper_x]
uart_pin: PC13
interpolate: True
run_current: 0.8
sense_resistor: 0.110
stealthchop_threshold: 0
diag_pin: ^PF4
driver_SGTHRS: 90

# y-stepper (A-Motor)
[stepper_y]
step_pin: PE2
dir_pin: PE1
enable_pin: !PE4
microsteps: 32
rotation_distance: 40
endstop_pin: ^PF3
full_steps_per_rotation:200
position_min: -20
position_endstop: 350
position_max: 350
homing_speed: 50
homing_retract_dist: 25
homing_positive_dir: true

[tmc2209 stepper_y]
uart_pin: PE3
interpolate: True
run_current: 0.8
sense_resistor: 0.110
stealthchop_threshold: 0

# z-stepper
# z0 stepper (Front Left on Motor3)
[stepper_z]
step_pin: PB8
dir_pin: PB7
enable_pin: !PE0
rotation_distance: 40
gear_ratio: 80:16
microsteps: 64
endstop_pin: probe:z_virtual_endstop
position_max: 340
position_min: -5
homing_speed: 25
second_homing_speed: 3
homing_retract_dist: 0

[tmc2209 stepper_z]
uart_pin: PB9
interpolate: true
run_current: 0.9
sense_resistor: 0.110
stealthchop_threshold: 0

# z1 stepper (Rear Left on Motor4)
[stepper_z1]
step_pin: PB4
dir_pin: !PB3
enable_pin: !PB6
rotation_distance: 40
gear_ratio: 80:16
microsteps: 64

[tmc2209 stepper_z1]
uart_pin: PB5
interpolate: true
run_current: 0.9
sense_resistor: 0.110
stealthchop_threshold: 0

# z2 stepper (Rear Right on Motor5)
[stepper_z2]
step_pin: PG13
dir_pin: PG12
enable_pin: !PG15
rotation_distance: 40
gear_ratio: 80:16
microsteps: 64

[tmc2209 stepper_z2]
uart_pin: PG14
interpolate: true
run_current: 0.9
sense_resistor: 0.110
stealthchop_threshold: 0

# z3 stepper (Front Right on Motor7)
[stepper_z3]
step_pin: PD4
dir_pin: !PD3
enable_pin: !PD6
rotation_distance: 40
gear_ratio: 80:16
microsteps: 64

[tmc2209 stepper_z3]
uart_pin: PD5
interpolate: true
run_current: 0.9
sense_resistor: 0.110
stealthchop_threshold: 0

# bed heater
[heater_bed]
##	SSR Pin - HE1
heater_pin: PA1
sensor_type: Generic 3950
sensor_pin: PB1
max_power: 1
min_temp: 0
max_temp: 125
#control: pid
#pid_kp: 58.437
#pid_ki: 2.347
#pid_kd: 363.769

# LED Control
[output_pin caselight_left]
#Chamber Lighting - HE2 Connector (Optional)
pin: PA0
pwm: true
shutdown_value: 0
value: 0.1
cycle_time: 0.01

[output_pin caselight_right]
#Chamber Lighting - HE2 Connector (Optional)
pin: PA3
pwm: true
shutdown_value: 0
value: 0.1
cycle_time: 0.01

# Homing and Gantry Adjustment Routines
[idle_timeout]
timeout: 1800
    
[quad_gantry_level]
gantry_corners:
    -60,-10
    410,420
points:
    25, 0
    25, 280
    325, 280
    325, 0
speed: 100
horizontal_move_z: 3
retries: 10
retry_tolerance: 0.0075
max_adjust: 10

# additional pinouts
[board_pins]
aliases:
    # EXP1 header
    EXP1_1=PE7, EXP1_2=PG1,
    EXP1_3=PG0, EXP1_4=PF15,
    EXP1_5=PF14, EXP1_6=PF13,    # Slot in the socket on this side
    EXP1_7=PF12, EXP1_8=PF11,
    EXP1_9=<GND>, EXP1_10=<5V>,
    
    # EXP2 header
    EXP2_1=PE13, EXP2_2=PE12,
    EXP2_3=PE15, EXP2_4=PE11,
    EXP2_5=PE10, EXP2_6=PE14,      # Slot in the socket on this side
    EXP2_7=PE8, EXP2_8=<RST>,
    EXP2_9=<GND>, EXP2_10=<NC>
    
# Exclude print objects & Firmware Retraction & Skew Correction
[exclude_object]

[firmware_retraction]

[skew_correction]

[gcode_preprocessor idle_tool_shutdown]
idle_timeout_minutes: 2
initial_feedrate: 3000

# Input Shaper
[input_shaper]

#[shaketune]
#result_folder: ~/printer_data/config/ShakeTune_results
#number_of_results_to_keep: 10
#keep_raw_data: True
#show_macros_in_webui: True
#timeout: 600
#measurements_chunk_size: 2
#max_freq: 200
#dpi: 300

# Bed Mesh Config for KAMP
[bed_mesh]
speed: 600
horizontal_move_z: 5
mesh_min: 25, 32
mesh_max: 325, 325
probe_count: 50, 50
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

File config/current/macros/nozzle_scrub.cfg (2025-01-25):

#####################################################################
# 	Nozzlewiper
#####################################################################

[gcode_macro CLEAN_NOZZLE]
#rename_existing: _CLEAN_NOZZLE
gcode:
  # home first in case printer is not
  {% if 'xyz' not in printer.toolhead.homed_axes %}
    SAFE_HOME
  {% endif %}

  _CLEAN_NOZZLE

[gcode_macro _CLEAN_NOZZLE]

# If you are putting your purge bucket at the rear left of the bed as per default installation, enable True on your location_bucket_rear 
# variable. If you want to put your purge bucket elsewhere (perhaps the front), then set it to False. See diagrams and description 
# further below on how to set your XY position.
variable_location_bucket_rear:      False

# If you want the purging routine in your bucket enabled, set to True (and vice versa).
variable_enable_purge:              False

# These parameters define your filament purging. The retract variable is used to retract right after purging to prevent unnecessary
# oozing. Some filament are particularly oozy and may continue to ooze out of the nozzle for a second or two after retracting. The
# ooze dwell variable makes allowance for this. Update as necessary. If you decided to not enable purge, you can ignore this section.
variable_purge_len:            10	         ; Amount of filament, in mm, to purge.
variable_purge_spd:           300	         ; Speed, in mm/min, of the purge.
variable_purge_temp_min:      220	         ; Minimum nozzle temperature to permit a purge. Otherwise, purge will not occur.
variable_purge_ret:             2            ; Retract length, in mm, after purging to prevent slight oozing. Adjust as necessary.
variable_ooze_dwell:            2            ; Dwell/wait time, in seconds, after purging and retracting.

# Adjust this so that your nozzle scrubs within the brush. Currently defaulted to be a lot higher for safety. Be careful not to go too low!
variable_brush_top:            3 

# These parameters define your scrubbing, travel speeds, safe z clearance and how many times you want to wipe. Update as necessary. Wipe 
# direction is randomized based off whether the left or right bucket is randomly selected in the purge & scrubbing routine.
variable_clearance_z:           7	         ; When traveling, but not cleaning, the clearance along the z-axis between nozzle and brush.
variable_wipe_qty:              7	         ; Number of complete (A complete wipe: left, right, left OR right, left, right) wipes.
variable_prep_spd_xy:        18000	         ; Travel (not cleaning) speed along x and y-axis in mm/min.
variable_prep_spd_z:         1500	         ; Travel (not cleaning) speed along z axis in mm/min.
variable_wipe_spd_xy:        12000	         ; Nozzle wipe speed in mm/min.


# These parameters define the size of the brush. Update as necessary. A visual reference is provided below. Note that orientation of 
# parameters remain the same whether bucket is at rear or front.
# 
#                  ←   brush_width   →                            
#                   _________________                                                          ↑
#                  |                 |  ↑                     If you chose location_bucket_rear = True, Y position is acquired
#  brush_start (x) |                 | brush_depth            from your stepper_y position_max. Adjust your brush physically in
#                  |_________________|  ↓                               Y so that the nozzle scrubs within the brush.       
#                          (y)                                                                 ↓
#                      brush_front
# __________________________________________________________
#                     PRINTER FRONT
# 
# 
## For V2.4 300mm build, uncomment this below:
variable_brush_start:     81

# This value is defaulted from brush location in CAD (rear left). Change if your brush width is different.
variable_brush_width:     36

## These are only used if location_bucket_rear is False. You specify a custom location in y axis for your brush - see diagram above. ##
variable_brush_front:       -16          
variable_brush_depth:       10          


# These parameters define the size of your purge bucket. Update as necessary. If you decided to not enable purge, you can ignore 
# this section. A visual reference is provided below. Note that orientation of parameters remain the same whether bucket is at rear 
# or front.
# 
#                                     bucket_gap
#                                      ← ---- →
#                     __________________________________________
#                    |                 |      |                 |      
#                    |                 |      |                 |
#  bucket_start (x)  |                 |______|                 |
#                    |                 |      |                 |
#                    |                 |      |                 |
#                    |_________________|. . . |_________________|
#                     ← ------------- →        ← ------------- →
#                     bucket_left_width        bucket_right_width
#  _______________________________________________________________________________________
#                                    PRINTER FRONT
# 

## For V2.4 300mm build, uncomment below
variable_bucket_left_width:    25

# These values are defaulted from bucket geometry in CAD (rear left location). Change only if you're using a custom bucket.
variable_bucket_right_width:   25            
variable_bucket_gap:           22	

# For V1.8, you may need to measure where your bucket start is and input into bucket_start. Otherwise, a value of 0 is for a default
# installation of purge bucket at rear left.
variable_bucket_start: 25


###############################################################################################################################################
###############################################################################################################################################

### From here on, unless you know what you're doing, it's recommended not to change anything. Feel free to peruse the code and reach out to me
### (edwardyeeks#6042) on Discord if you spot any problems!

###############################################################################################################################################
###############################################################################################################################################

# Placeholder. The variable will later be set to contain, at random, a number representing the left or right bucket.
variable_bucket_pos:            1
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

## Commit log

2024-11-27 Added first printfiles for picam and panellatch
    [NewLatch-5.0mm.stl, VoronZPiCamMount11.stl]
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2024-12-01 Added sample configs for M8P
    [Voron2_M8P-v1.0_config.cfg, Voron2_M8P-v1.1_config.cfg, Voron2_M8P-v2.0_config.cfg]
2024-12-01 Added printfiles for Z-Drives. Z-Idlers & Z-Endstop
    [[a]_belt_tensioner_a_x2.stl, [a]_belt_tensioner_b_x2.stl, [a]_z_drive_baseplate_a_x2.stl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]
2024-12-01 Added 3MF file for Z-Drives
    [z-drive.3mf]
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2024-12-01 Updated printed part list and 3MF
    [z-drive.3mf]
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2024-12-05 Added 3MF for z-idler & nozzle_probe
    [nozzle_probe.3mf, z-idler.3mf]
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2024-12-09 Added front idler printfiles
    [[a]_tensioner_left.stl, [a]_tensioner_right.stl, front_idler_left_lower.stl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]
2024-12-09 Added 3MF for front idlers
    [front-idlers.3mf]
2024-12-10 Added printfiles for AB Drives
    [[a]_cable_cover.stl, [a]_z_chain_retainer_bracket_x2.stl, a_drive_frame_lower.stl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]
2024-12-10 Added 3MF for ab drive units
    [ab-drive-units.3mf]
2024-12-10 Added printfiles for XY Joints
    [[a]_endstop_pod_D2F_switch.stl, [a]_endstop_pod_hall_effect.stl, [a]_xy_joint_cable_bridge_2hole.stl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]
2024-12-10 Added 3MF for XY Joints
    [xy-joints.3mf]
2024-12-11 Added printfiles for Gantry
    [[a]_z_belt_clip_lower_x4.stl, [a]_z_belt_clip_upper_x4.stl, z_chain_bottom_anchor.stl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]
2024-12-11 Added 3MF for Gantry
    [gantry.3mf]
2024-12-11 Update for XY Joints
    [xy-joints.3mf]
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2024-12-12 Added printfiles for Z-Joints
    [z_joint_lower_x4.stl, z_joint_upper_hall_effect.stl, z_joint_upper_x4.stl]
2024-12-12 Added 3MF for Z-Joints
    [z_joints.3mf]
2024-12-12 Added tools to printfiles
    [MGN12_rail_guide_x2.stl, MGN9_rail_guide_x2.stl, bed_hole_marking_template_x1_Rev2.STL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]
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2024-12-12 Update 3MF for tools
    [tools.3mf]
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2024-12-23 Added printer.cfg and update README
    [printer.cfg]
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2024-12-24 Fixed motor pins for Z
    [printer.cfg]
2024-12-24 Homing speed and separate macros to own file
    [macros.cfg, printer.cfg]
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2024-12-25 Set correct motor position
    [printer.cfg]
2024-12-25 Fixed motor movement & change z_hop for safe_home
    [printer.cfg]
2024-12-25 Raised homing speed & z_endstop_calibrate
    [printer.cfg]
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2024-12-25 Unnecessary entries removed, notes on unfinished config removed
    [printer.cfg]
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2024-12-25 Added print files for doors
    [Door_Handle_x1.STL, door_hinge_x6.stl, doors.3mf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]
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2024-12-25 Added printfiles for bottom panel
    [bottom_panel_clip_x4.stl, bottom_panel_clips.3mf, bottom_panel_hinge_x2.stl]
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2024-12-25 Adjust probe speed and QDL horizontal move
    [printer.cfg]
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2024-12-26 Fixed Extruder
    [ebb36.cfg]
2024-12-26 Raised Retries for QDL
    [printer.cfg]
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2024-12-27 Changed position of bed heating on print start
    [macros.cfg]
2024-12-27 Changed run_current and microsteps for Z
    [printer.cfg]
2024-12-27 Adjustments after first print
    [macros.cfg, printer.cfg]
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2024-12-27 Added print files to mods
    [Chain link 30 degree angle.stl, Chain link 40 degree angle.stl, Chain link 55 degree angle.3mf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]
2024-12-28 Added nozzlewiper (by MarcFair)
    [macros.cfg, printer.cfg, wipenozzle.cfg]
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2024-12-30 Added printfiles for hotend mounts
    [Bambu_Mount.stl, RapidoHF_Mount.stl]
2025-01-08 Input Shaper & Bed Mesh
    [printer.cfg]
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2025-01-10 PID Tuning & Input Shaper
    [printer.cfg]
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2025-01-11 Fixed value for line_purge
    [ebb36.cfg]
2025-01-11 Changed print_start and print_end macro
    [macros.cfg, printer.cfg]
2025-01-12 Config sync Printer => GitHub
    [ebb36.cfg, fans.cfg, macros.cfg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]
2025-01-12 Adjust toolhead position for wiping start
    [wipenozzle.cfg]
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2025-01-16 Added filament runout sensor
    [ebb36.cfg]
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2025-01-21 Added controller fans to print_start & print_end
    [macros.cfg]
2025-01-21 Added for testing new nozzle wiper
    [nozzle_scrub.cfg, printer.cfg]
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2025-01-25 Fixed brush front
    [nozzle_scrub.cfg]
2025-01-25 New Sherpa Mini files
    [Sherpa_Mini.3mf, filament_sensor_housing_sherpa_mini.stl, rear_housing_sherpa_mini_for filament sensor.stl]
2025-01-25 Changes on Dragon Burner
    [dragonburner.3mf]
2025-01-26 Fixed G32
    [macros.cfg]
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2025-02-01 Added straight brace for Dragon Burner
    [Brace_Straight.stl]
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2025-02-01 Added TEST_SPEED macro from Ellis
    [macros.cfg]
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2025-02-01 Added new values for Input Shaper
    [printer.cfg]
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2025-02-02 Changed position for first G28 in PRINT_START
    [macros.cfg]
2025-02-10 Update config & macros
    [ebb36.cfg, macros.cfg, nozzle_scrub.cfg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]
2025-02-12 Added first printfiles for Toolchanger
    [DragonBurner.stl, NozzelPadClip-Dragon.stl, Nozzle Pad Mold A.stl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]
2025-02-12 Added printfiles for Tapchanger
    [Backplate.stl, Cowling.stl, EBB36 Shield.stl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]
2025-02-13 Added additional print files
    [6mm belt clip x2.stl, Housing.3mf, Left Side.stl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]
2025-02-16 Added printfiles and input shaper
    [XEndstop Lever v3.step, XEndstop Lever v3.stl, tapchanger - toolboard.3mf]
2025-02-16 Added supportclips for PTFE Tube and CANBus-Cable
    [support_clips.3mf]
2025-02-17 Added possible mountplate for sherpa mini
    [sherpa_mini.stl]
2025-02-18 Added printfiles for Stealthchanger
    [6mm belt clip x2.stl, Backplate.stl, Cowling.stl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]
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2025-03-17 Fixed params_safe_y
    [th0.cfg, th1.cfg, toolchanger.cfg]
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2025-03-19 Correct variable name
    [macros.cfg]
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2025-03-21 Set correct heater
    [th0.cfg, th1.cfg]
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2025-03-24 Toolhead indepent on print_start to start with every toolhead if needed
    [macros.cfg]
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2025-03-24 Fixed position error
    [macros.cfg]
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2025-04-04 Correct params_park
    [th0.cfg, th1.cfg]
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2025-04-12 Fixed gcode_z_offset, docj positions & z_offset
    [th0.cfg, th1.cfg, th2.cfg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]
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2025-04-12 correct offset position
    [th2.cfg, th3.cfg, th4.cfg]
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2025-04-18 Z-Offset after TC-Nozzle for alle Toolheads und new param_park
    [printer.cfg, th0.cfg, th1.cfg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]
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2025-04-22 Correct z_offset between toolheads
    [macros.cfg, printer.cfg, th0.cfg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]
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2025-04-23 Fixed nameing issue
    [macros.cfg]
2025-04-23 Removed new G28 and added CLEAR_PROBE to print_start
    [macros.cfg]
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2025-09-22 Fixed bedfan macro for toolchanger
    [fans.cfg]
2025-09-22 Z-Offset, GCode_Z_Offset and fixed an error
    [th0.cfg, th1.cfg, th2.cfg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]
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2025-09-26 Correct gcode_z_offset
    [th1.cfg, th2.cfg, th3.cfg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]
2025-09-26 Fix for sensorless issue on X
    [printer.cfg]
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2026-01-01 Added nozzle cleaner & new backplate for Dragon Burner
    [DragonBurner parts - BackPlate v3.step, voron-24-front-nozzle-wiper-mount-v3.step]
